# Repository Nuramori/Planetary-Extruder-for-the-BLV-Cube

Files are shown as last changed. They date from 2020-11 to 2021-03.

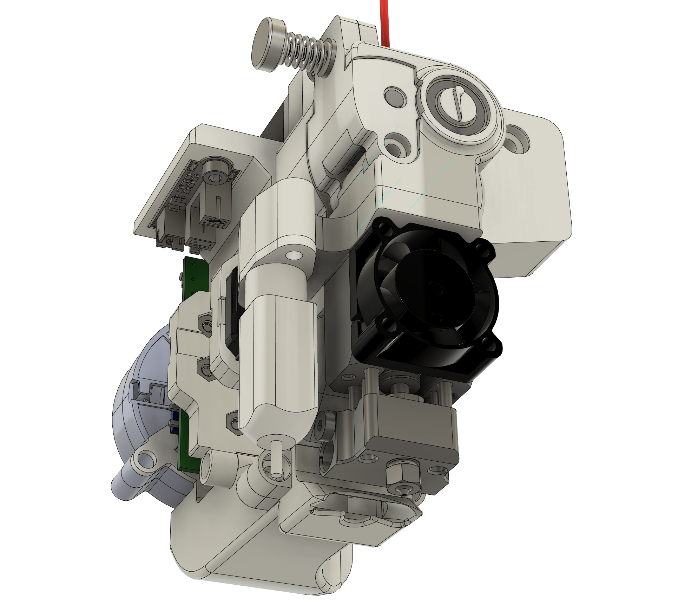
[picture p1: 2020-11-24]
Images/Standard Mosquito Hotend Component Orientation.png

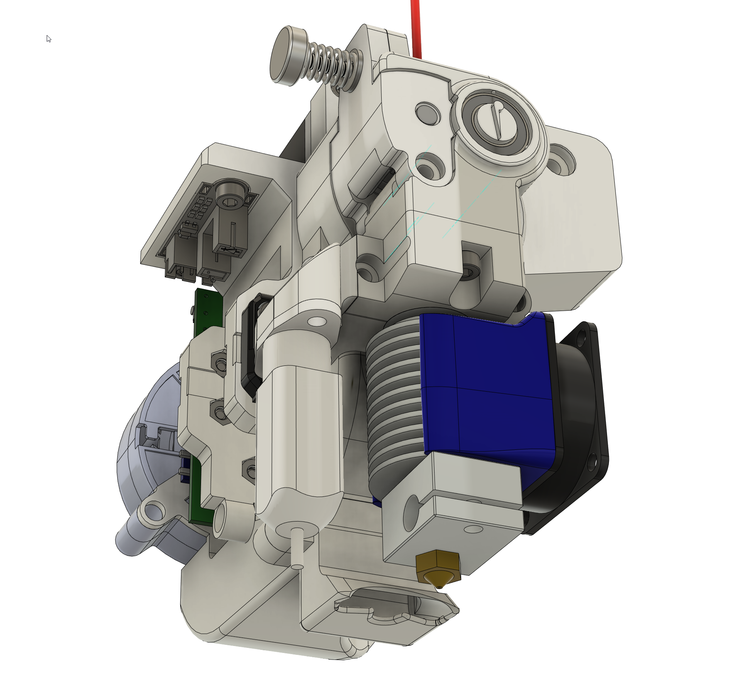
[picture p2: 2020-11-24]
Images/E3D Hotend Component Orientation.png

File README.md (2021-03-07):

# Planetary Extruder for the BLV Cube - The EdP-Drive.

<B><br />This work is licensed under a <a rel="license" href="http://creativecommons.org/licenses/by-sa/4.0/">Creative Commons Attribution-ShareAlike 4.0 International License</a>.</B>

This is an extruder design specifically for the BLV Cube, with a branch modified for the BLV metal carrier upgrade.  Key design concepts that drove the design direction were the following:

Implement a geared reduction drive to allow for a smaller and lighter stepper motor, that offsets the motor's lower torque with the torque increase of a planetary drive system, combined with a helical gear ratio to reach a final ratio of 12:1

Utilize a BLTouch as the z-axis prober.

Allow for multiple hotend types by basing attachments via a simple adapter plate and parts cooler nozzle change.  Allow swaps with a couple of screws/bolts.

Electronics support to be integrated into the shell carrier.

A future release will be more universal with a blank backplate for modification to adapt to other carrier/printer needs.

If you wish to look around in a web browser, here are some links.

Integrated Version : https://a360.co/2Vma0a4<BR>
Metal/universal version : https://a360.co/36IUueP
<br>

# UPDATE v1.04 [March 6, 2021]

Thanks to a fellow BLV owner that's building a metal carrier version with the toolboard, there was an additional tweak necessary if people were to use the experimental belt retainers that come with the metal kit.  It also needed fixing... 

I still plan on doing another update that has the installation/construction sequence to make it easier for people to assemble the extruder.
<br>
<br>

# UPDATE v1.03 [March 4, 2021]

Thanks to a fellow BLV owner that's building a metal carrier version with the toolboard, I found a few errors that needed fixing... 
<br>
<br>

# UPDATE v1.02 [March 3, 2021]

Added a new blower frame for the metal carrier to accommodate the Duet Toolboard up to board version 1.0 (current as of this update).
<br>
<br>

# UPDATE v1.01 [January 14, 2021]

I added new adapters; one specifically for the for the metal carrier variation, to accommodate the Mosquito (air-cooled) and the other for the Dragon hotend from TriangleLabs.  The Dragon Adapter is complete for both the integrated and metal carriers.

I plan on doing an update soon that has the installation/construction sequence to make it easier for people to assemble things :p.
<br>
<br>

# FIRST RELEASE v1.0 [Dec 25, 2020]

The project has been printed and tested, with a few minor tweaks.  I'm formally calling it the EdP-Drive, or "P-Drive" if you wish.  I also have released this under a new licensing terms, to allow for community development, and open to commercial USE.  I would as anyone that utilizes this design, extend the courtesy of proper credits for the work and expense put into bringing this work to the community.  Thanks.

<B>Non-Printed Parts List</B>

<B>Extruder Motor</B><BR>
<B>Type&emsp;&emsp;&emsp;&ensp;&ensp;Manufacturer&emsp;&emsp;&ensp;&ensp;Part No.</B>          
NEMA11&nbsp;&nbsp;&nbsp;&nbsp;&nbsp;&nbsp;&nbsp;&nbsp;Moons Industries&nbsp;&nbsp;&nbsp;&nbsp;&nbsp;&nbsp;MS11HS1P4100   

<B>Source :</B>     Moons Industries<BR>
<B>Link :</B>       https://www.moonsindustries.com/p/nema-11-standard-hybrid-stepper-motors/ms11hs1p4100-000004611110015846<BR><BR>

<B>Bearings<BR>
Type&emsp;&emsp;&emsp;&emsp;Quantity&emsp;&emsp;Use/Purpose</B>                   
B695ZZ&emsp;&emsp;&nbsp;&nbsp;one (1)&emsp;&emsp;&emsp;&ensp;Motor spindle support<BR>
B676ZZ&emsp;&emsp;&nbsp;&nbsp;three (3)&emsp;&emsp;&emsp;Planetary gears<BR>
MR148ZZ&emsp;&nbsp;&nbsp;&nbsp;three (3)&emsp;&emsp;&nbsp;&nbsp;&nbsp;Planetary carrier and driven sun gear drive support<BR>

<B>Source :     Misumi, Amazon</B><BR>
<B>Misumi :</B>&emsp;https://us.misumi-ec.com/vona2/detail/110300107560/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<BR>
<B>Misumi :</B>&emsp;https://us.misumi-ec.com/vona2/detail/110300107560/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<BR>
<B>Amazon :</B>&emsp;https://www.amazon.com/uxcell-MR148ZZ-Groove-Bearings-Shielded/dp/B082PPPSPT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<BR><BR>

<B>Hobbed Gears<BR>
Type&emsp;&emsp;&emsp;&emsp;&emsp;&emsp;&emsp;&emsp;&emsp;&nbsp;Quantity&emsp;&emsp;&emsp;Detail</B><BR>
BondTech Drive Gears&emsp;&emsp;one (1)&emsp;&emsp;&emsp;&nbsp;&nbsp;1.75mm Filament, 8mm Shaft size

Source :     Filastruder<BR>
Link :       https://www.filastruder.com/collections/bondtech/products/drivegear-kit?variant=12119193124935
<BR><BR>

<B>Clamp Thumbscrew Tensioner<BR>
Type&emsp;&emsp;&emsp;&emsp;&emsp;&emsp;&emsp;&emsp;&emsp;&emsp;&emsp;&emsp;&emsp;&emsp;&emsp;&nbsp;Quantity&emsp;&emsp;&emsp;</B><BR>
BondTech Thumbscrew Tensioner&emsp;&emsp;&emsp;one (1)&emsp;&emsp;&emsp;&nbsp;&nbsp;

Source :     Filastruder<BR>
Link :       https://www.filastruder.com/collections/bondtech/products/bondtech-thumbscrew-assembly
<BR>
<BR>  

<B>Optical Endstop</B><BR>
Type&emsp;&emsp;&emsp;&emsp;&emsp;&emsp;&emsp;&emsp;&emsp;&emsp;&emsp;&emsp;&emsp;&emsp;&emsp;&nbsp;Quantity&emsp;&emsp;&emsp;Manufacturer</B><BR>
Optical      one (1)       Lerdge

Source:      Amazon
Link:        https://www.amazon.com/Printer-Accessories-Optical-Tachometer-Photoelectric/dp/B088P3TPCB
alternate:   https://www.amazon.com/MakerHawk-Optical-Endstop-Photoelectric-Control/dp/B07PMW2QMT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
<BR>
<BR>  
  
<B>Fan</B><BR>
Type&emsp;&emsp;&emsp;&emsp;&emsp;&emsp;&emsp;&emsp;&emsp;&nbsp;Quantity&emsp;&emsp;&emsp;Detail</B><BR>
5015         one (1)    12v Dual ball bearing

Source :     Amazon
Link :       https://www.amazon.com/WINSINN-Bearing-50x15mm-Turbine-Brushless/dp/B07WFJV28K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<BR><BR>

<B>BLTouch offset values for listed adapters:</B><BR>
The default x,y offsets are x=-25, y=0 unless noted otherwise.<BR>

<B>Current adaptors using this default are as follows:</B><BR>
Slice Engineering Mosquito standard<BR>
Slice Engineering Copperhead<BR>
E3D V6<BR>
Nova<BR>
  
<B>Unique offsets are as follows:</B><BR>
Mosquito Liquid :&nbsp;&nbsp;&nbsp;&nbsp;&nbsp;&nbsp;&nbsp;x=0, y=-20<BR><BR>
  
<B>Configuring steps/mm</B><BR>  
Since the extruder utilizes gear reduction to 12:1 to increase torque, the steps/mm need to be adjusted.  <B>Based on a 0.8degree motor, it is recommended the base value be set to 1299.</B><BR>

The standard method of calibrating extruder steps is recommended to fine tune this value to suit your machine.

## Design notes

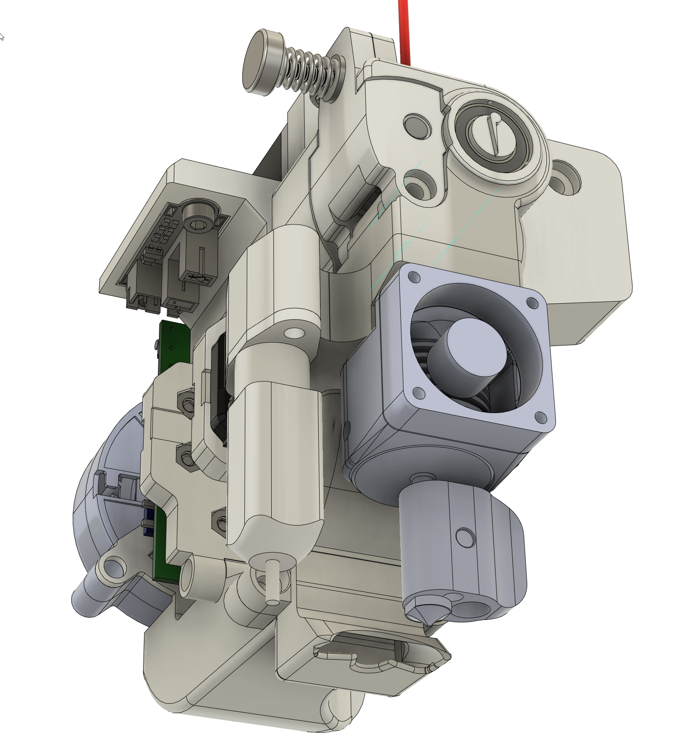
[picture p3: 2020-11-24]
Images/Nova Hotend Orientation.png

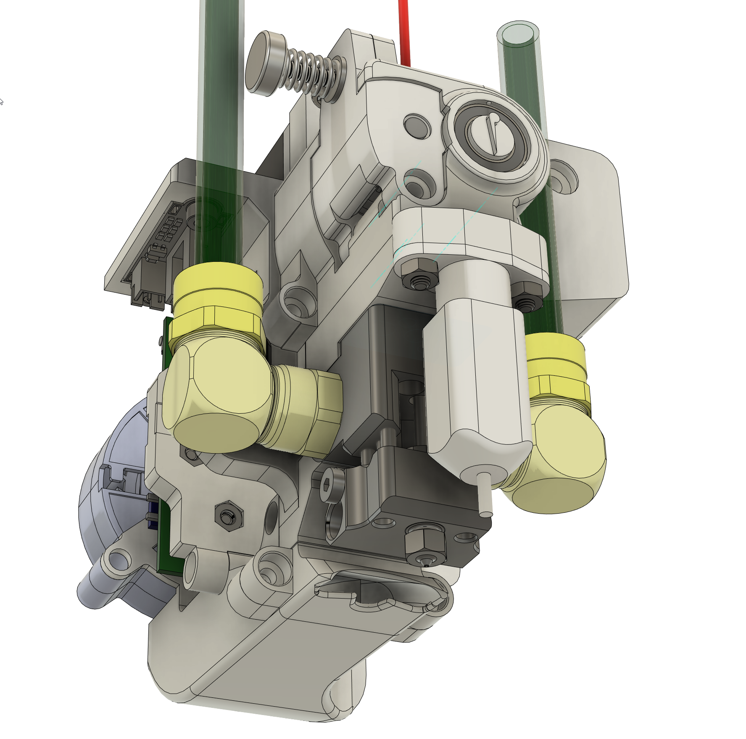
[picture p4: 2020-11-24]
Images/Mosquito Liquid Hotend Orientation.png

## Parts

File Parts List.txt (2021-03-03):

The following parts are needed for this build.  Included are links and/or item numbers and their sources that I have used to complete this project.
Note that sources other than what I have used may result in variances in tolerance that are out of my control, and may require some consideration if
you explore other avenues to acquire the items listed.

Extruder Motor
Type         Manufacturer        Part No.          
NEMA11       Moons Industries    MS11HS1P4100   

Source :     Moons Industries
Link :       https://www.moonsindustries.com/p/nema-11-standard-hybrid-stepper-motors/ms11hs1p4100-000004611110015846

Bearings
Type         Quantity            Use/Purpose                   
B695ZZ       one (1)             Motor spindle support
B676ZZ       Three (3)           Planetary gears
MR148ZZ      Three (3)           planetary carrier & Driven Sungear support

Source :     Misumi, Amazon
Links :      https://us.misumi-ec.com/vona2/detail/110300107560/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
             https://us.misumi-ec.com/vona2/detail/110300107560/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
             https://www.amazon.com/uxcell-MR148ZZ-Groove-Bearings-Shielded/dp/B082PPPSPT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

Hobbed Gears
Type                     Quantity            Detail
BondTech Drive Gears     1                   1.75mm Filament, 8mm Shaft size

Source :     Filastruder
Link :       https://www.filastruder.com/collections/bondtech/products/drivegear-kit?variant=12119193124935

Optical Endstop (Integrated variant)
Type         Quantity      Manufacturer
Optical      one (1)       Lerdge

Source:      Amazon
Link:        https://www.amazon.com/Printer-Accessories-Optical-Tachometer-Photoelectric/dp/B088P3TPCB
alternate:   https://www.amazon.com/MakerHawk-Optical-Endstop-Photoelectric-Control/dp/B07PMW2QMT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

Fan
Type         Quantity   Detail
5015         one (1)    12v Dual ball bearing

Source :     Amazon
Link :       https://www.amazon.com/WINSINN-Bearing-50x15mm-Turbine-Brushless/dp/B07WFJV28K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

Screws & nuts
Integrated Design

Metal Carrier Design

Printed Build Parts:

Part name             Quantity      Basis of Design Material              Basis of Design Print Method   Basis of Design Print Source   May be FDM Printed
Back Shell            one (1)       GBPA12 (Glass Bead filled Nylon 12)   MJF                            Jawstec.com                    No
                      *Back shell for the metal carrier version can be PA12

Front Shell           one (1)       PA12 (Nylon 12)                       MJF                            Jawstec.com                    Not Recommended
Filament Clamp        one (1)       PA12 (Nylon 12)                       MJF                            Jawstec.com                    Yes

Planetary Carrier     one (1)       GBPA12 (Glass Bead filled Nylon 12)   MJF                            Jawstec.com                    No
Planetary Gear        three (3)     GBPA12 (Glass Bead filled Nylon 12)   MJF                            Jawstec.com                    No
Fixed Ring Gear       one (1)       GBPA12 (Glass Bead filled Nylon 12)   MJF                            Jawstec.com                    No
Driven Sun Gear       one (1)       GBPA12 (Glass Bead filled Nylon 12)   MJF                            Jawstec.com                    No
Pinion Gear           one (1)       GBPA12 (Glass Bead filled Nylon 12)   MJF                            Jawstec.com                    No

Belt Clamps           four (4)      PA12 (Nylon 12)                       MJF                            Jawstec.com                    Yes

Blower Frame          one (1)       PA12 (Nylon 12)                       MJF                            Jawstec.com                    Not Recommended
Blower nozzle         one (1)       GBPA12 (Glass Bead filled Nylon 12)   MJF                            Jawstec.com                    Not Recommended

Hotend Adaptor(s)     one (1)       GBPA12 (Glass Bead filled Nylon 12)   MJF                            Jawstec.com                    Recomend MJF, but can be printed.

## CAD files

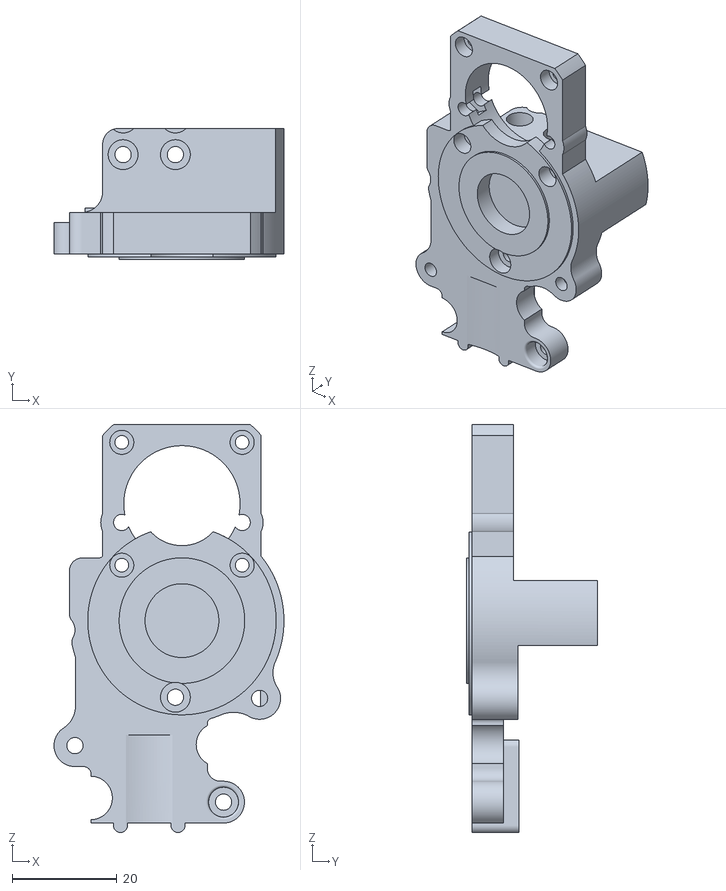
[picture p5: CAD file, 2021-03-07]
BLV Metal Carrier/EDP Planetary Vertical - Back Shell - Metal Carrier.stl
43.9 x 25.0 x 78.0

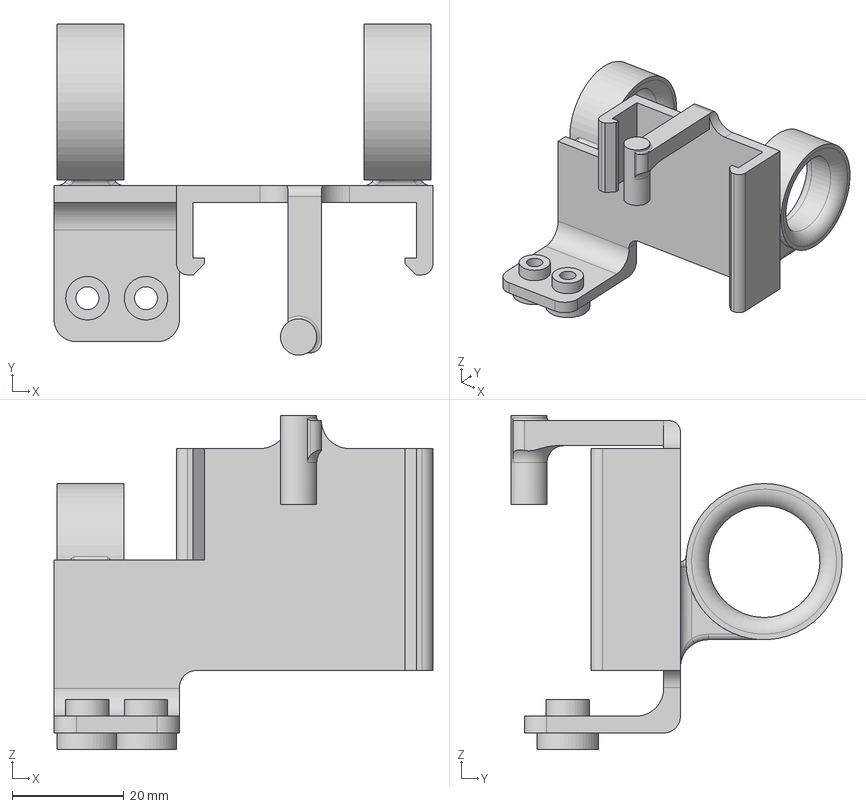
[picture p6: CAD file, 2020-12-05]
Common Components/EDP Planetary Vertical Cooling Block support - Integrated.step
68.0 x 59.4 x 60.0 mm

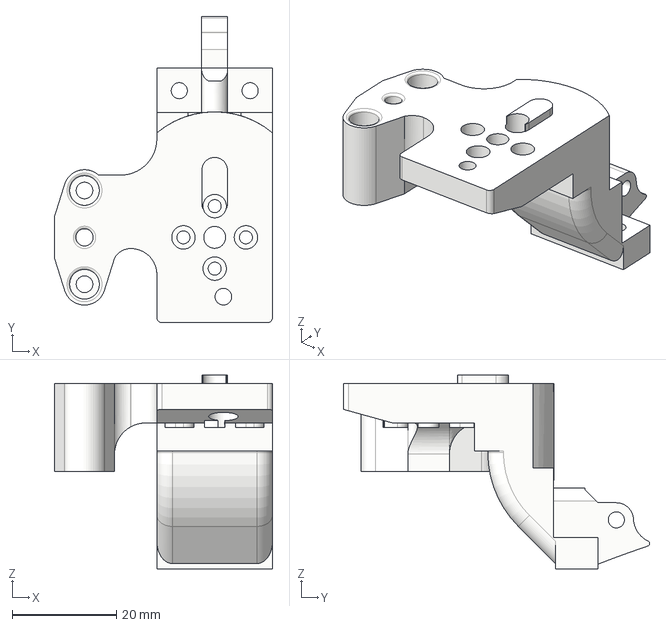
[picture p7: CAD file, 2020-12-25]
Hotend Adapters and Nozzles/Copperhead/Integrated Carrier/EDP Planetary Vertical - Copperhead Adapter - Integrated.step
41.9 x 58.8 x 37.2 mm

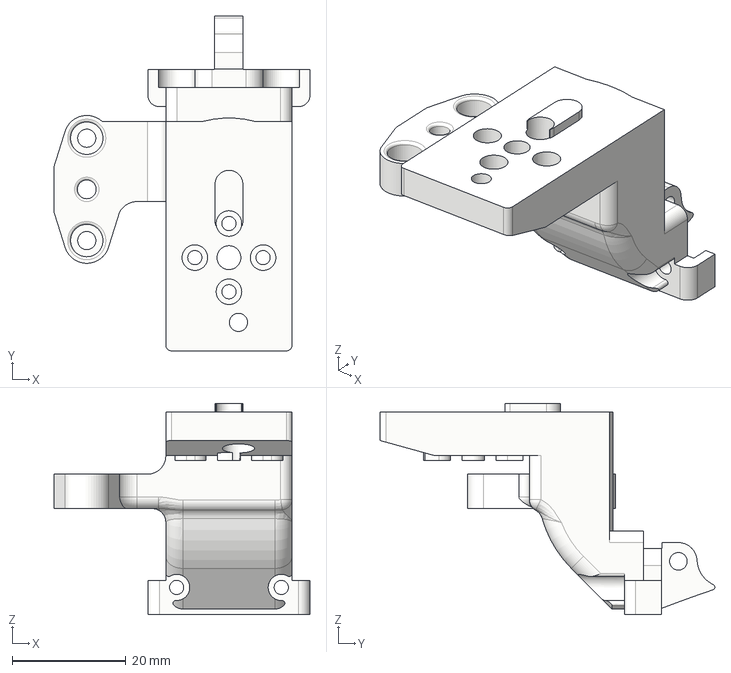
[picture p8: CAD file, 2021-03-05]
Hotend Adapters and Nozzles/Copperhead/Metal Carrier/EDP Planetary Vertical - Copperhead adaptor - Metal Carrier.step
45.0 x 58.8 x 37.2 mm

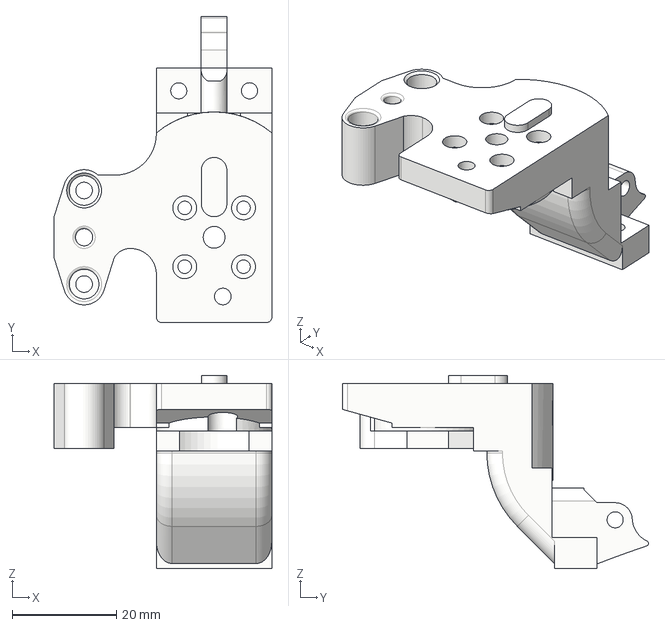
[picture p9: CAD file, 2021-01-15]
Hotend Adapters and Nozzles/Dragon/Integrated Carrier/Planetary Vertical - Dragon Adapter - Integrated.step
41.9 x 58.8 x 37.2 mm

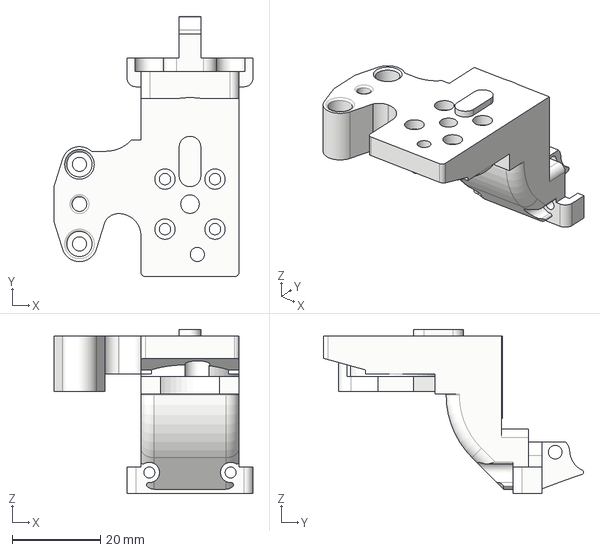
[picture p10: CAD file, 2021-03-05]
Hotend Adapters and Nozzles/Dragon/Metal Carrier/Planetary Vertical - Dragon Adapter - Metal Carrier.step
45.0 x 58.8 x 37.2 mm

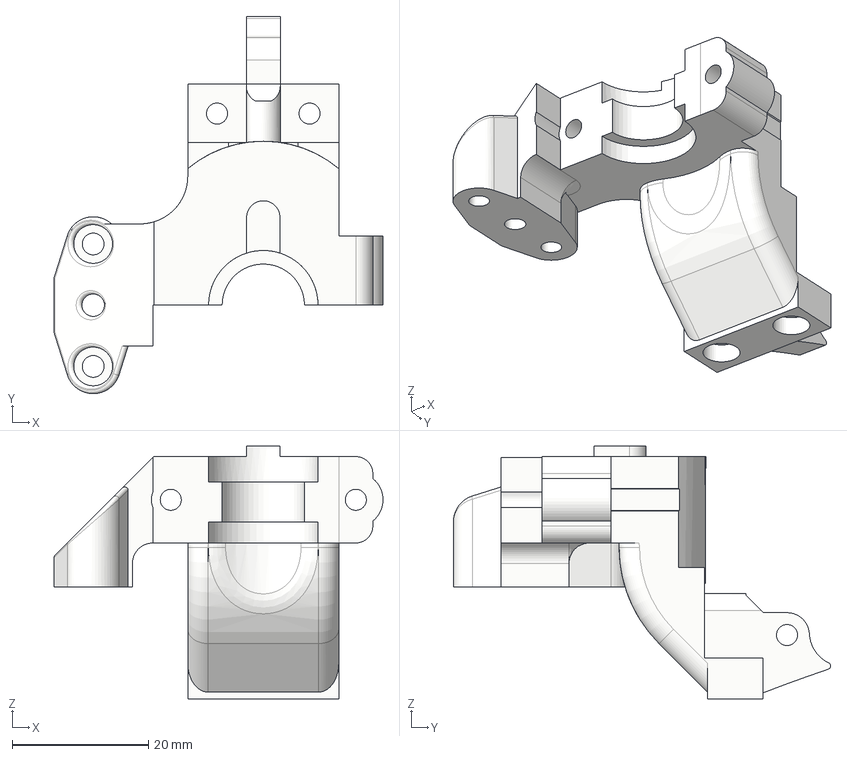
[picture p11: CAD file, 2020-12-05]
Hotend Adapters and Nozzles/E3D v6 (groove mount)/Integrated Carrier/EDP Planetary Vertical - E3D Back Adapter - Integrated.step
48.4 x 55.5 x 37.2 mm

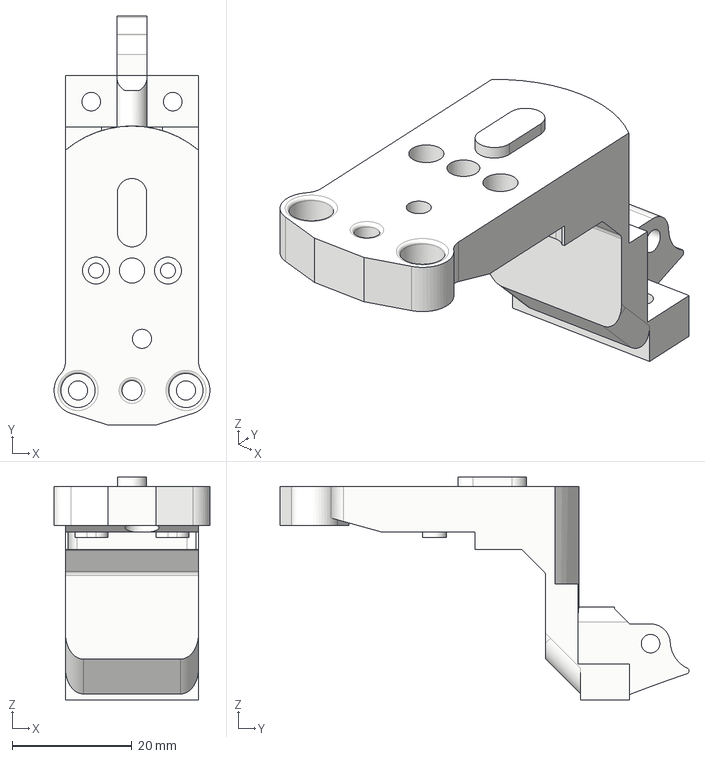
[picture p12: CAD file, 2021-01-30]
Hotend Adapters and Nozzles/Mosquito Liquid/Integrated Carrier/EDP Planetary Vertical liquid Adapter - Integrated.step
26.0 x 68.2 x 37.2 mm

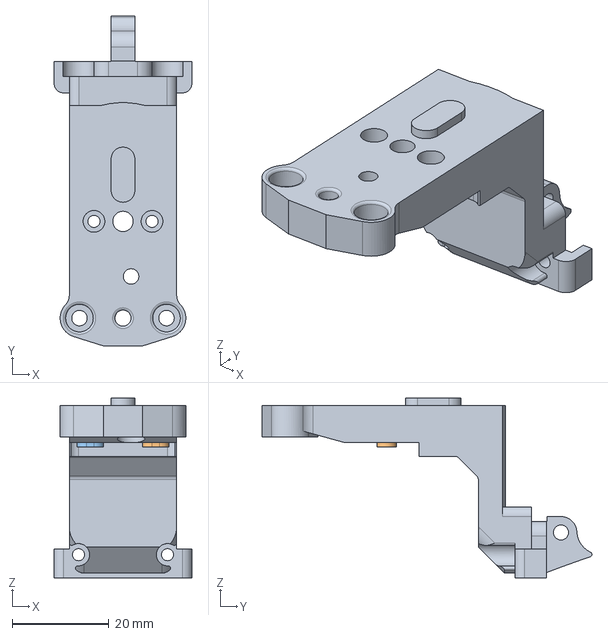
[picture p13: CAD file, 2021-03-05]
Hotend Adapters and Nozzles/Mosquito Liquid/Metal Carrier/EDP Planetary Vertical - Liquid adaptor - Metal Carrier.step
28.5 x 68.2 x 37.2 mm

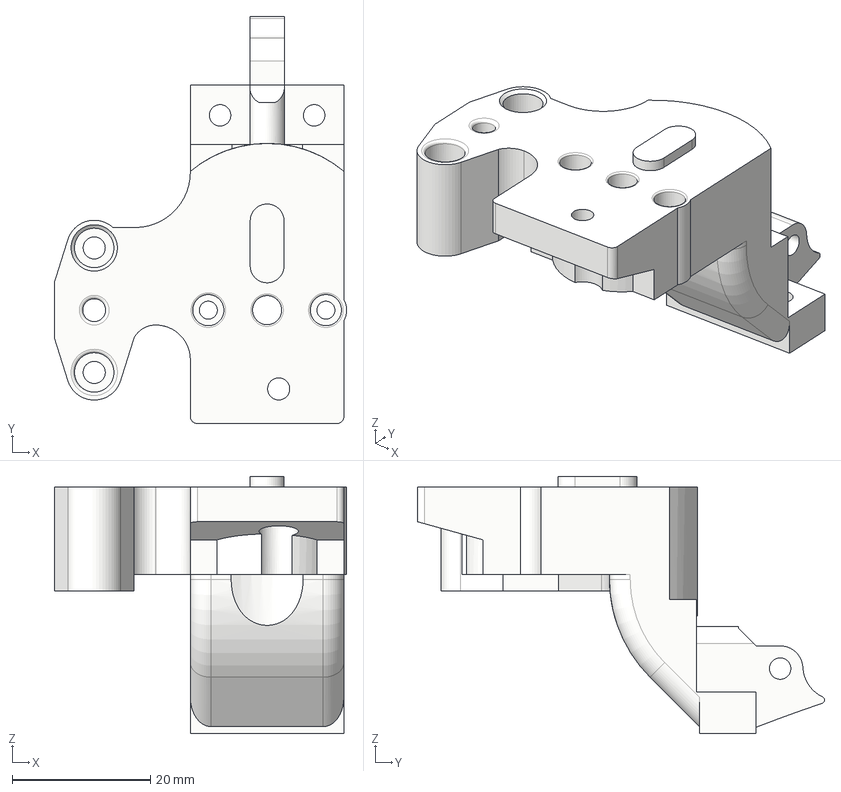
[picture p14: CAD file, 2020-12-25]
Hotend Adapters and Nozzles/Nova/Integraged Carrier/EDP Planetary Vertical - Nova Adapter - Integrated.step
42.3 x 58.8 x 37.2 mm

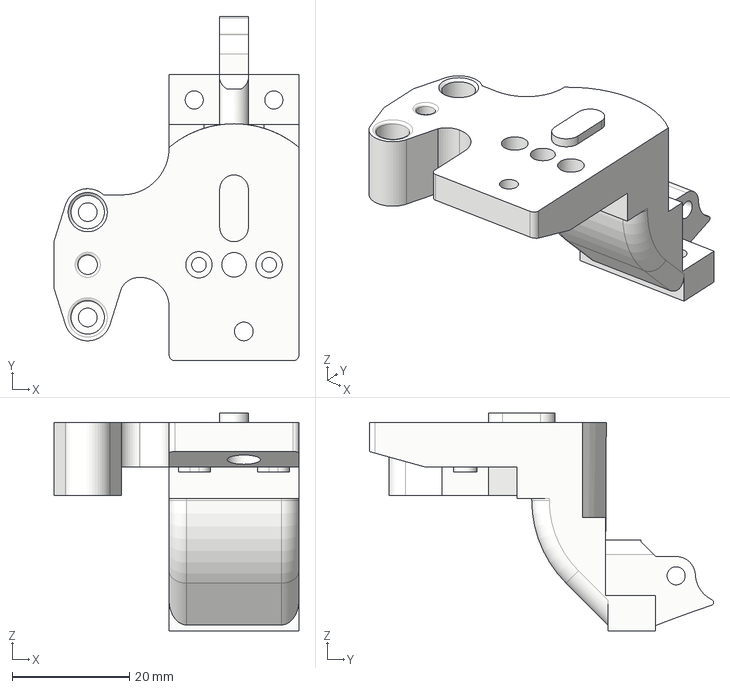
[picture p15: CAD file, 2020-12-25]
Hotend Adapters and Nozzles/Standard Mosquito (air cooled)/Integrated Carrier/EDP Planetary Vertical - Standard Mosquito Adapter - Integrated.step
41.9 x 58.8 x 37.2 mm

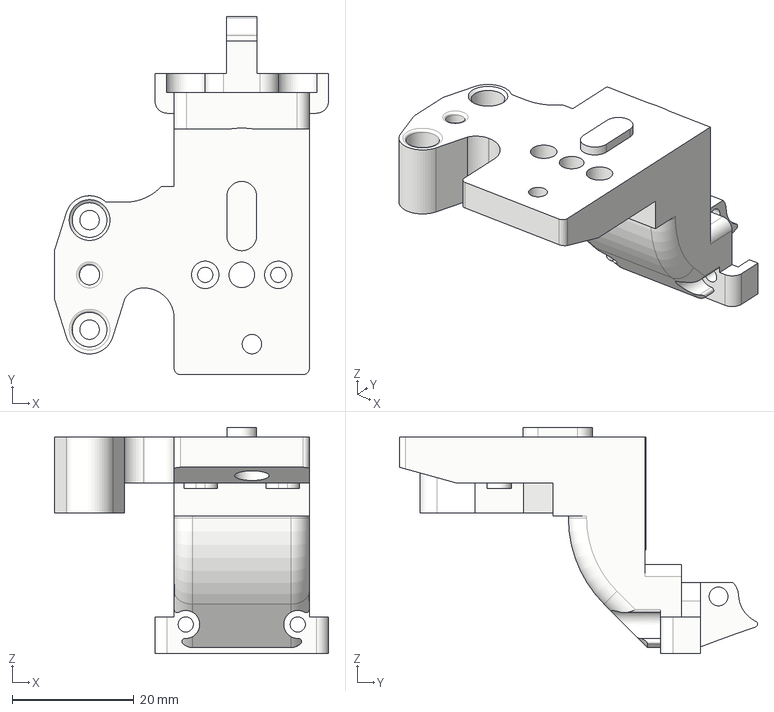
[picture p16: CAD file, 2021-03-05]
Hotend Adapters and Nozzles/Standard Mosquito (air cooled)/Metal Carrier/Planetary Vertical - Mosquito Adapter - Metal Carrier.step
45.0 x 58.8 x 37.2 mm

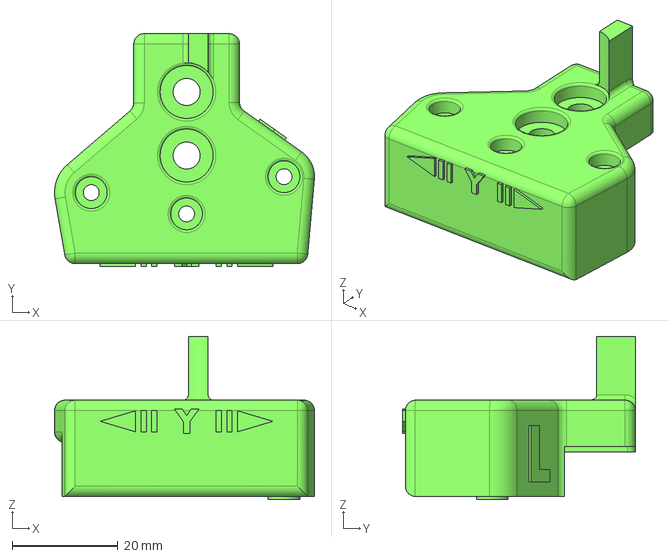
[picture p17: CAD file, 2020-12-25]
Integrated Carrier/Optical Endstop Trigger Gantry Top - BLV.step
49.1 x 43.9 x 30.8 mm

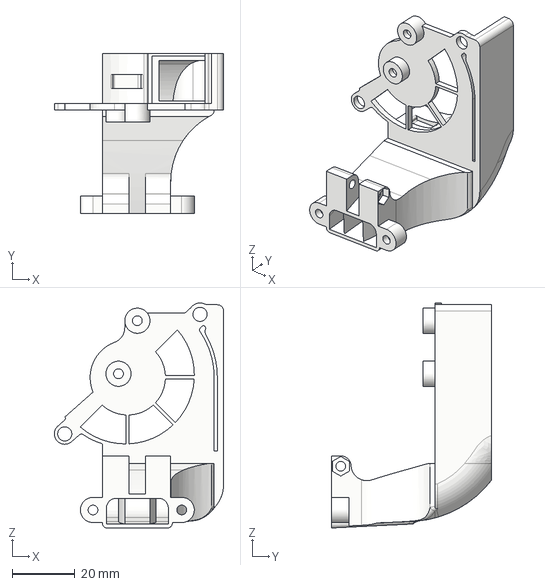
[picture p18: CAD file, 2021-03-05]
BLV Metal Carrier/EDP Planetary Vertical - metal carrier_Planetary Vertical - No electronics blower frame.step
53.8 x 51.0 x 71.5 mm

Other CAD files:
Common Components/EDP Planetary Vertical - Pinion Drive Gear - Common.stl
Hotend Adapters and Nozzles/Copperhead/Integrated Carrier/EDP Planetary Vertical - Copperhead Nozzle - Integrated.step
Hotend Adapters and Nozzles/Copperhead/Metal Carrier/EDP Planetary Vertical - Copperhead Nozzle - Metal Carrier.step
Hotend Adapters and Nozzles/Dragon/Integrated Carrier/EDP Planetary Vertical - Dragon Nozzle - Integrated.step
BLV Metal Carrier/EDP Planetary Vertical - metal carrier_Planetary Vertical - Toolboard blower frame.step
BLV Metal Carrier/EDP Planetary vertical - Optical Endstop Adapter.step
Common Components/EDP Planetary Vertical - Belt Clamp 1 of 4 - Common.step
Common Components/EDP Planetary Vertical - clamp body - Common.stl
Hotend Adapters and Nozzles/Dragon/Metal Carrier/EDP Planetary Vertical - Dragon Nozzle - Integrated.step
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

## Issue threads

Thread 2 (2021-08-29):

Instalation

milicigoran, 2021-08-29:
Is there a file to show you how to put together printed parts?

SneakyPete36, 2021-08-29:
Ed made installation guideline but can’t find the a link or something to the source only have a screenshot of it from his post on the BLV MgN Group at Facebook.
If you’re in the group you could search for Ed’s name and find it somewhere in all his his posts.

SneakyPete36, 2021-08-29:
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

Nuramori, 2021-08-29:
I’ll finish up the guide and put it on the GitHub.

Sent from my iPhone

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

milicigoran, 2021-09-14:
> Ed made installation guideline but can’t find the a link or something to the source only have a screenshot of it from his post on the BLV MgN Group at Facebook.
> If you’re in the group you could search for Ed’s name and find it somewhere in all his his posts.

sweet thank you. one more question is there a Dyze hotend for it? would love to push a lot of filament through the dyze with a 0.6n nozzle and going up to 500c. im just finishing my build now for the blv cube because i started doing the rat rig vcast idex at the same time and half way through i got tired of everyone talking about their voron and got one of those also. so i don't know where i want to  put your extruder but i know i like it a lot. might go on more than one printer. I bought 2 ldo steppers like the orbiter and that metal 3 gear thing. now to  just put it together.

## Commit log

2020-11-23 Create Planetary Vertical Front Shell - Integrated.stl
2020-11-23 Create Planetary Vertical Front Shell - Metal Carrier.stl
2020-11-23 Create Planetary Vertical - Mosquito Adapter - Integrated.step
    [Planetary Vertical - Mosquito Adapter - Integrated.step]
2020-11-23 Create Planetary Vertical Copperhead Adapter - Integrated.step
    [Planetary Vertical Copperhead Adapter - Integrated.step]
2020-11-23 Preliminary release development
    [Planetary Vertical - Mosquito Adapter - Integrated.step, Planetary Vertical Copperhead Adapter - Integrated.step]
2020-11-23 Preliminary development release
    [Planetary Vertical - Mosquito Adapter - Integrated.step, Planetary Vertical Copperhead Adapter - Integrated.step, Planetary Vertical Copperhead Nozzle.step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]
2020-11-23 Create Blower Frame.stl
2020-11-23 Create Pinion Drive - 0,75M 12t.stl
2020-11-23 Create Ring Drive.stl
2020-11-23 Create Belt Clamp.stl
    [Belt Clamp.stl]
2020-11-23 Copperhead adapter plate
    [Copperhead Nozzle.step]
2020-12-03 Deleted based on actual Liquid hotend product
    [Mosquito Liquid bottom - Integrated.step, Mosquito liquid Adapter top Universal.step, Planetary Vertical liquid Adapter - Integrated.step]
2020-12-03 Revert "Deleted based on actual Liquid hotend product"
    This reverts commit 6200b3b3d679cf853a1d12e0d17c115eb6c513d8.
    [Mosquito Liquid bottom - Integrated.step, Mosquito liquid Adapter top Universal.step, Planetary Vertical liquid Adapter - Integrated.step]
2020-12-03 Revert "Revert "Deleted based on actual Liquid hotend product""
    This reverts commit fbdf31268c47675aeb843e7b225c93780d748771.
    [Mosquito Liquid bottom - Integrated.step, Mosquito liquid Adapter top Universal.step, Planetary Vertical liquid Adapter - Integrated.step]
2020-12-03 Revised to accommodate actual end product
    [Mosquito liquid Adapter - Integrated.step]
2020-12-05 Major correction - deleted file to be replpaced shortly
    [Mosquito Liquid bottom - metal carrier.step, Mosquito liquid Adapter - Integrated.step, Mosquito liquid Adapter top Universal.step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]
2020-12-05 BETA v0.8
    Reorganized the tree, corrected the gearing ratio, and simplified the planetary transmission. Created a cartridge design for the front half to increase reliability and ease of maintenance.
    [Belt Clamp.stl, Copperhead Adapter - Integrated.step, Copperhead Nozzle.step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]
2020-12-05 BETA v0.8
    [EDP Planetary Vertical - metal carrier_Planetary Vertical - No electronics blower frame.step, EDP Planetary Vertical Cooling Block support - Integrated.step]
2020-12-18 Update EDP Planetary Vertical - Planetary Carrier - Common.stl
2020-12-25 Final update for first release
    [EDP Planetary Vertical - Back Shell - Metal Carrier.stl, EDP Planetary Vertical - Copperhead Adapter - Integrated.step, EDP Planetary Vertical - Copperhead ada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]
2020-12-25 First Public Release
    [Optical Endstop Trigger Gantry Top - BLV.step]
2021-01-14 Added Mosquito (air) adapter for the metal carrier
    [Planetary Vertical - Mosquito Adapter - Metal Carrier.step]
2021-01-15 Added Dragon Adapter
    [Planetary Vertical - Dragon Adapter - Integrated.step, Planetary Vertical - Dragon Adapter - Metal Carrier.step]
2021-01-15 Added Nozzles for the Dragon
    [EDP Planetary Vertical - Dragon Nozzle - Integrated.step, EDP Planetary Vertical - Standard Mosquito Nozzle -Metal Carrier.step]
2021-01-30 Slight tweak, nothing critical.
    [EDP Planetary Vertical - Liquid Adapter - Integrated.step, EDP Planetary Vertical liquid Adapter - Integrated.step]
2021-03-03 Create EDP Planetary Vertical - metal carrier_Planetary Vertical - Toolboard blower frame.step
    Blower frame to accommodate the Duet Toolboard
    [EDP Planetary Vertical - metal carrier_Planetary Vertical - Toolboard blower frame.step]
2021-03-04 Update EDP Planetary Vertical - metal carrier_Planetary Vertical - Toolboard blower frame.step
    Fixed a minor problem with the toolboard frame
    [EDP Planetary Vertical - metal carrier_Planetary Vertical - Toolboard blower frame.step]
2021-03-05 Corrections to the metal carrier parts related to the blower frame and adapters.
    There were some small dimensional errors with a hole size, as well as an alignment with the nozzle face outlet.
    [EDP Planetary Vertical - metal carrier_Planetary Vertical - No electronics blower frame.step, EDP Planetary Vertical - metal carrier_Planetary Vertical - Toolb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]
2021-03-07 Slight update to the back shell on the metal carrier version
    Since the experimental belt retainers were not available, a fellow BLV owner that's beta testing has share dimensional info that led to the refinement.
    [EDP Planetary Vertical - Back Shell - Metal Carrier.stl]
